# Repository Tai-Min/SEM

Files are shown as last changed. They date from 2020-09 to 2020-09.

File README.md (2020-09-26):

# Simple Enclosure Manager
This little board allows you to control your 3d printer's enclosure using physical buttons or MQTT (using scripts, [Domoticz](https://www.domoticz.com/), [Home assistant](https://www.home-assistant.io/) or [Octoprint](https://octoprint.org/) events). The target software for this board is [Tasmota](https://tasmota.github.io/docs/).

PCB

## Features
* Powered by 12V power supply,
* Based on ESP-12E,
* Two 12V controllable outputs designed to control enclosure's LEDs and carbon filter fan , 1.5A total, supports PWM,
* One mains relay for printer's power supply, up to 10A at 230V,
* Three button inputs to control LEDs, carbon filter fan and printer's PSU directly
* 12V power connector secured for overvoltage, reverse voltage and by 2A ressetable fuse,
* Mains power connector secured for overvoltage and by 10A fast fuse.

## Assembly
### Get the board
The board is rather too hard to be etched (thin traces and small vias) so I would suggest using services of some PCB manufacturer to make it.<br/>

### Soldering
When you get the board and required components, start soldering smallest SMD components such as resistors and capacitors, then solder ESP-12 module and THT components. Finish the job by soldering connectors, buttons and relay.

## Uploading the firmware
For flashing the firmware you would need some USB to UART converter, or you can use NodeMCU to act as one.
#### WARNING This board uses 3.3V voltage level so make sure that choosen USB to UART converter also uses 3.3V as higher voltages such as 5V will fry the board and let the magic smoke out.

#### WARNING Before flashing the firmware make sure that the board is not connected to any other power source such as 12V

Also, you need to remove "GPIO 3" jumper before proceeding further.

### Using the converter
Simply connect the converter to the board:
* VCC <-> 3.3V
* Gnd <-> Gnd
* Rx <-> Tx
* Tx <-> Rx

Then put your device into programming mode by holding "FLASH" button and then pressing "RESET" button. After a while release the "FLASH" button. Now the device is in flash mode.

Now, all you need to do is to flash Tasmota firmware into your board. Easiest method to do this is to use [Tasmotizer](https://tasmota.github.io/docs/Getting-Started/#flashing).
### Using NodeMCU
Short EN pin to GND and simply connect it to the board:
* 3.3V <-> 3.3V
* Gnd <-> Gnd
* Tx <-> Tx
* Rx <-> Rx

Then put your device into programming mode by holding "FLASH" button and then pressing "RESET" button. After a while release the "FLASH" button. Now the device is in flash mode.

Now, all you need to do is to flash Tasmota firmware into your board. Easiest method to do this is to use [Tasmotizer](https://tasmota.github.io/docs/Getting-Started/#flashing).

## Examples
All of the examples listed here require a priori knowledge about used programs.
### Simple mosquitto script
<TODO>

### Octoprint events
<TODO>

### Hassio integration
<TODO>

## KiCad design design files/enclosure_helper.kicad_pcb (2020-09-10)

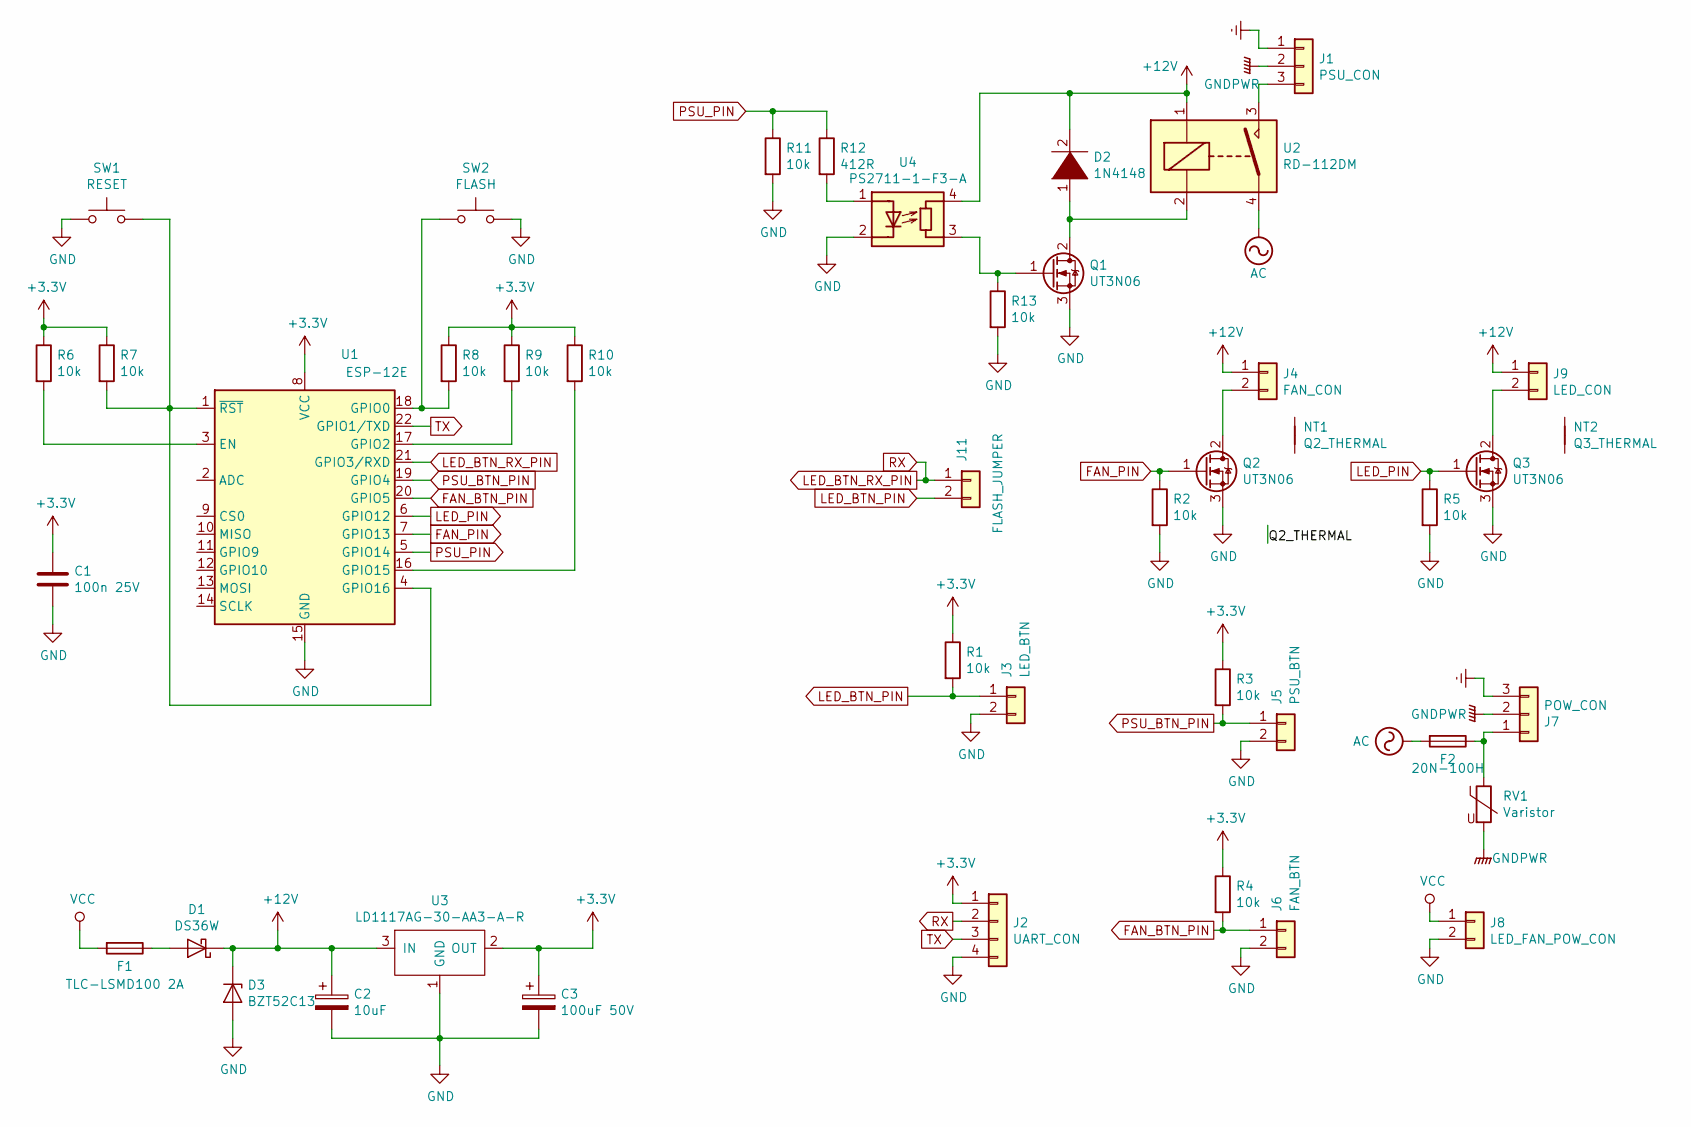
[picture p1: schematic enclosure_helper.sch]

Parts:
C1: 100n 25V; C_1206_3216Metric_Pad1.42x1.75mm_HandSolder
C2: 10uF; CP_Elec_6.3x5.4
C3: 100uF 50V; CP_Elec_8x10.5
D1: DS36W; D_SOD-123
D2: 1N4148; D_DO-35_SOD27_P7.62mm_Horizontal
D3: BZT52C13; D_SOD-123
F1: TLC-LSMD100 2A; Fuse_2920_7451Metric_Pad2.10x5.45mm_HandSolder
F2: 20N-100H; R_Axial_DIN0411_L9.9mm_D3.6mm_P5.08mm_Vertical
J1: PSU_CON; PhoenixContact_MSTBA_2,5_3-G-5,08_1x03_P5.08mm_Horizontal
J2: UART_CON; PinHeader_1x04_P2.54mm_Vertical
J3: LED_BTN; BarrelJack_Wuerth_6941xx301002
J4: FAN_CON; BarrelJack_Wuerth_6941xx301002
J5: PSU_BTN; BarrelJack_Wuerth_6941xx301002
J6: FAN_BTN; BarrelJack_Wuerth_6941xx301002
J7: POW_CON; PhoenixContact_MSTBA_2,5_3-G-5,08_1x03_P5.08mm_Horizontal
J8: LED_FAN_POW_CON; PhoenixContact_MSTBA_2,5_2-G_1x02_P5.00mm_Horizontal
J9: LED_CON; BarrelJack_Wuerth_6941xx301002
J11: FLASH_JUMPER; PinHeader_1x02_P2.54mm_Vertical
NT1: Q2_THERMAL; NetTie-2_SMD_Pad0.5mm
NT2: Q3_THERMAL; NetTie-2_SMD_Pad0.5mm
Q1: UT3N06; SOT-89-3_Handsoldering
Q2, Q3: UT3N06; TO-251-3-1EP_Horizontal_TabDown
R1, R2, R3, R4, R5, R6, R7, R8, R9, R10, R11, R13: 10k; R_1206_3216Metric_Pad1.42x1.75mm_HandSolder
R12: 412R; R_1206_3216Metric_Pad1.42x1.75mm_HandSolder
RV1: Varistor; RV_Disc_D12mm_W6.7mm_P7.5mm
SW1: RESET; SW_PUSH_6mm
SW2: FLASH; SW_PUSH_6mm
U1: ESP-12E
U2: RD-112DM; RD_112DM
U3: LD1117AG-30-AA3-A-R; SOT-223
U4: PS2711-1-F3-A; SOP-4_3.8x4.1mm_P2.54mm

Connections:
+3V3: C1.1, C3.1, J2.1, R1.1, R3.1, R4.1, R6.1, R7.1, R8.1, R9.1, R10.1, U1.8 (VCC), U3.2 (OUT)
+12V: C2.1, D1.1 (K), D2.2 (A), D3.1 (K), J4.1, J9.1, U2.1, U3.3 (IN), U4.4 (R)
AC: F2.2, U2.4
Earth: J1.1, J7.3
FAN_BTN_PIN: J6.1, R4.2, U1.20 (GPIO5)
FAN_PIN: Q2.1 (G), R2.1, U1.7 (GPIO13)
GND: C1.2, C2.2, C3.2, D3.2 (A), J2.4, J3.2, J5.2, J6.2, J8.2, Q1.3 (S), Q2.3 (S), Q3.3 (S), R2.2, R5.2, R11.2, R13.2, SW1.1, SW2.2, U1.15 (GND), U3.1 (GND), U4.2 (K)
GNDPWR: J1.2, J7.2, RV1.2
LED_BTN_PIN: J3.1, J11.2, R1.2
LED_BTN_RX_PIN: J2.2, J11.1, U1.21 (GPIO3/RXD)
LED_PIN: Q3.1 (G), R5.1, U1.6 (GPIO12)
unnamed: D1.2 (A), F1.1
unnamed: D2.1 (K), Q1.2 (D), U2.2
unnamed: F2.1, J7.1, RV1.1
unnamed: J1.3, U2.3
unnamed: J4.2, Q2.2 (D)
unnamed: J9.2, Q3.2 (D)
unnamed: NT1.1, Q3.4
unnamed: NT2.1, Q2.4
unnamed: Q1.1 (G), R13.1, U4.3 (R)
unnamed: R6.2, U1.3 (EN)
unnamed: R7.2, SW1.2, U1.1 (~RST), U1.4 (GPIO16)
unnamed: R8.2, SW2.1, U1.18 (GPIO0)
unnamed: R9.2, U1.17 (GPIO2)
unnamed: R10.2, U1.16 (GPIO15)
unnamed: R12.2, U4.1 (A)
PSU_BTN_PIN: J5.1, R3.2, U1.19 (GPIO4)
PSU_PIN: R11.1, R12.1, U1.5 (GPIO14)
TX: J2.3, U1.22 (GPIO1/TXD)
VCC: F1.2, J8.1

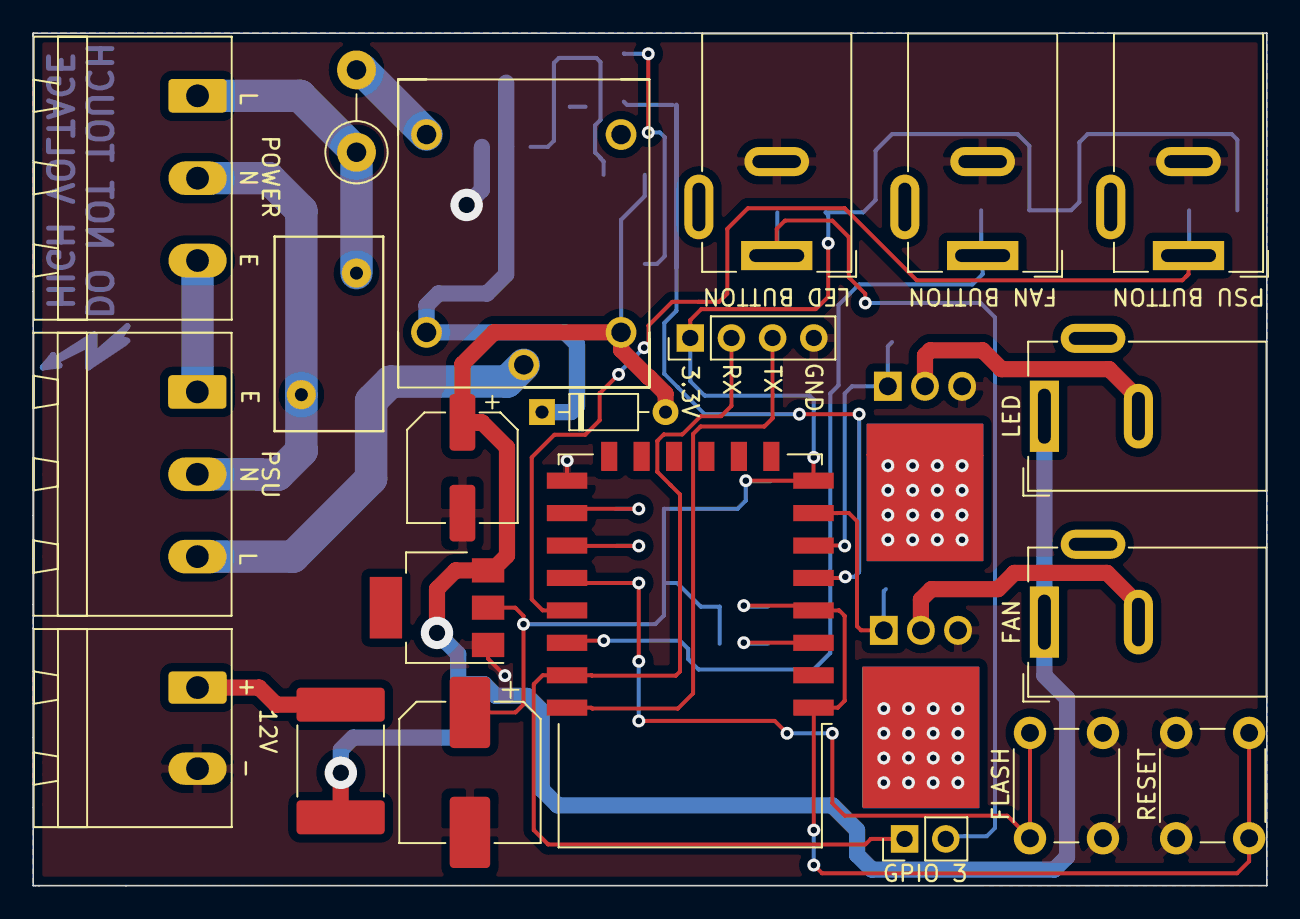
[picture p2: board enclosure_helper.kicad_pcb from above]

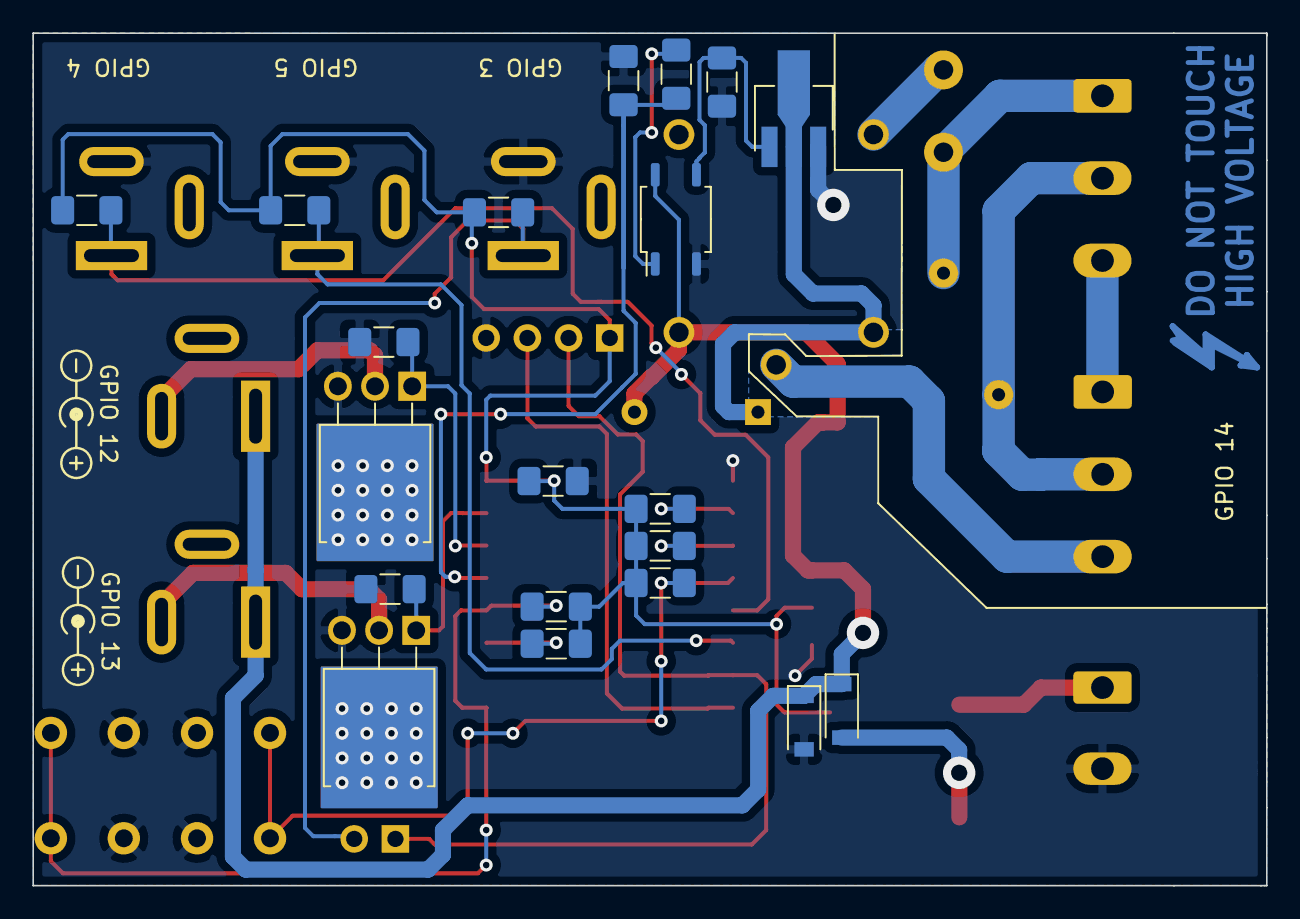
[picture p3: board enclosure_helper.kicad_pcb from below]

Board: 2 copper layers, 76.1 x 52.6 mm, 43 parts (20 on the bottom side), 30 nets.
